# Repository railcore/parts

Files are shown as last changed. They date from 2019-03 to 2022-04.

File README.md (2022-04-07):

Railcore II 300ZL/ZLT
=======

RailCore® II is a Core-XY based Reprap 3D printer designed by J. Steve White & Tony Akens under the CC-Attribution Only license. Please refer to the attribution file for other contributions.

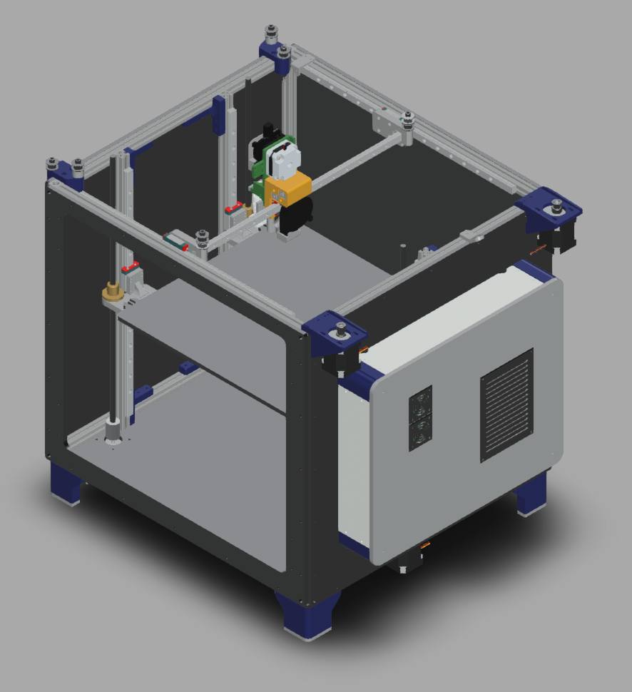
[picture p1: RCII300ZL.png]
Railcore


## Top-Level Specs
* CoreXY Motion System
* 300x300x300mm (ZL) or 300x300x600mm (ZLT) build volume.
* kinematically coupled bed plate (optionally)
* autotramming with 3-point bed-leveling
* ~$1700 for a single unit, including hotend. See the [BOM][bom] for the part breakdown
* User Extensible! We encourage extending the design to custom applications via custom tools and bed plates
* Full specs listed on [this page](https://railcore.org)

## Build your own Railcore

The best way to get started is to thumb through the [**Assembly Instructions**](https://railcore.dozuki.com/c/RailCore_II) and [**Bill of Materials**][bom] first. Then, your options are to self-source using the [BOM][bom], or purchase a kit. Kit options:

* https://www.filastruder.com/collections/railcore (US-Based, kits are comprised of exactly the parts on the [BOM][bom])
* https://hightemp3d.com (EU-Based, kits may not be comprised of the parts on the [BOM][bom])

## Repository Contents

* **DXF** - DXF files for the RailCore II 300ZL & ZLT, typically for sheet cutting. Materials that can be used are in a text materials.md file for viewing.
* **STEP**  - STEP files for the RailCore II 300ZL & ZLT. All printed parts, milled and cut parts.
* **STL**  - contains STL all the parts that need to be printed to produce a Railcore. Some, like Z-Brackets and Z-Yokes, are available in aluminum. See [BOM][bom].
* **auxillary**  - List of auxillary, untested or outdated parts for the RailCore II
  * **font** - contains the font used for the Railcore II 300ZL/ZLT engraving on the panels.
  * **jigs** - contains parts that can be used for alignment or assembly.
  * **print_tests** - contains parts that can be used for testing/tuning a Railcore
  * **outdated parts** - contains parts that are no longer used.
* **upgrade_or_crossgrade_parts** - for official parts that aren't necessary for a base RailCore functionality. (doors or STL's for commercial parts authorised by RailCore Labs)
* **wiring** - contains details on all the custom wiring that is used in a Railcore in WireViz format.

The halo and Y-plate are optional, the motor mount and idler mounts are recommended to be made from aluminum, but machined and finished versions are available, see [BOM][bom].
More printed parts are available at the [RailCore Thingiverse collection](https://www.thingiverse.com/railcore/collections/300zl-zlt)

## Support

Have questions? Building your own Railcore? **[Join the Discord!][discord]**
Lots more information available [here](https://railcore.org)

## Contributing

Railcore is meant to be extended by the community. If you are interested in contributing, there are a number of ways to get involved:

* Review, comment, or add to the **[open issues](https://github.com/railcore/parts/issues)**
* **[Join the Discord!][discord]**

### Open Source
The name Railcore is a registered trademark of RailCore Labs, LLC. All Rights reserved.
Railcore is licensed under a [Creative Commons Attribution-ShareAlike 3.0 Unported License][cc-by] (CC BY-SA 3.0).
[][cc-by]
You can modify / distribute these files, and as long as you attribute to RailCore Labs e.g. "Original design by RailCore Labs"

[bom]: https://docs.google.com/spreadsheets/d/1sxKl6h23SXfuNM7hNiX35rIrpISw8AruEEcNl2Fvibk/edit?usp=sharing
[cc-by]: https://creativecommons.org/licenses/by-sa/3.0/
[cc-by-image]: https://i.creativecommons.org/l/by-sa/3.0/88x31.png
[discord]: https://discord.gg/Sy569Hq
[wiki]: https://railcore.org

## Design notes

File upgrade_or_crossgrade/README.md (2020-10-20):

# Upgrade or Crossgrade Parts

This repo is for official parts that aren't necessary for a base RailCore functionality.

They may add functionality or improve appearance or provide different functionality from the base RailCore design, but are not necessary in any sense for building a RailCore. 

### Coupler Cover
This is a part designed to drop over the couplers to protect them from random detritus and tools - you know, the cruft in the bottom of your printer - from interfering or getting caught in your spinning Z couplers.

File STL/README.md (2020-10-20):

# Printed Parts

Here are the 3d printed parts necessary for a RailCore 2 printer. 

Some parts have been retired in favor of better alternatives from the community, and we recommend aluminum for the motor mounts, idler carriers, and X carriages; but the original designs still work and are archived here.

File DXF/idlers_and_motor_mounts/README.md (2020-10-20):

Aluminium & Printed idlers and motor mounts
Not needed if you have a halo

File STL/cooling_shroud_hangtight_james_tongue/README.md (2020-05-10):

Railcore V6 Part cooling Duct by Hangtight / James Tongue is licensed under the Creative Commons - Attribution - Non-Commercial license.
Railcore V6 Part cooling Duct V2 version with 3DCPrinting supports remixed by J.Steve White.
https://www.facebook.com/groups/RailCore/permalink/2262880700664343/

# Summary

A Beta part cooling duct for the Railcore 300ZL utilising a 5015 blower and proven nozzle geometry.

The adapter plate has a slot for a captive M3 nut, and the duct will require an insert/ helicoil for the blower retention bolt.

A duct version and adapter plate for the aluminium carriage plate added.

Both ducts revised to give an extra 2mm of height clearance. Spacers/shims added, and the F3d files are there for the adapters and shims.

http://creativecommons.org/licenses/by-nc/3.0/
http://www.thingiverse.com/thing:3367622

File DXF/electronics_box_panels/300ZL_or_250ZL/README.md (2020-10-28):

# 300ZL and 250ZL Electrobox

Some reorganization with a few changes:

* Removed unsightly vent holes from side panel of eBox
* Added snazzy ventilation to back panel for Astrydyne switch
* Added fancy fan holes to front panel
* Added bottom panel with cutouts for Z steppers (to keep fingers out of electronics)

Kits use HDPE largely; there are aluminum alternatives and lots of acrylic side panels out there. The original 250s were white melamine.

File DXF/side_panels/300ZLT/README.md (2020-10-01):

# ZLT Panels

*NB* : These files use the ../Electronics_Box! 

The *.dxf files here are exported from the base model.

Base panel includes bottom brace holes.
Right panel uses ZL Electrobox and has holes for Duet 2/Duex and Duet 3

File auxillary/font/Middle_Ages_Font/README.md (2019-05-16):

How to install this font on your computer
=========================================

For Windows 7 / Vista users:

- Right-click the font file(s) and choose "Install".

For users of the previous Windows versions:

- Copy the included file(s) into a default Windows font folder 
  (usually C:\WINDOWS\FONTS or C:\WINNT\FONTS)

For Mac users:

Mac OS X 10.3 or above (including the FontBook)

- Double-click the font file and hit "Install font" button at 
  the bottom of the preview.

Mac OS X

- Either copy the font file(s) to /Library/Fonts (for all users), 
  or to /Users/Your_username/Library/Fonts (for you only).

For Linux users:

- Copy the font file(s) to /USR/SHARE/FONTS

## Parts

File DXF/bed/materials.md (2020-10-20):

MIC6 or ACP5080P tool plate for the bed

0.6mm spring steel for the magnetic bed steel sheet.

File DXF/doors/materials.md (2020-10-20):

PC or clear acrylic for doors and covers
any plastic for the PSU & fan covers.

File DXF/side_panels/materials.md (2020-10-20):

Melamine MDF
Hardboard
Acrylic there are concerns it might crack around the bolts for mounting, washers may be advisable)
Masonite Pegboard
Plywood (hardwood such as birch is preferable. Plywood is deforms easily around bolts, washers and upgrading the “M3 x 10mm Hex head Bolts” to “M3 x 12mm Hex head Bolts” may be advisable)
Aluminum

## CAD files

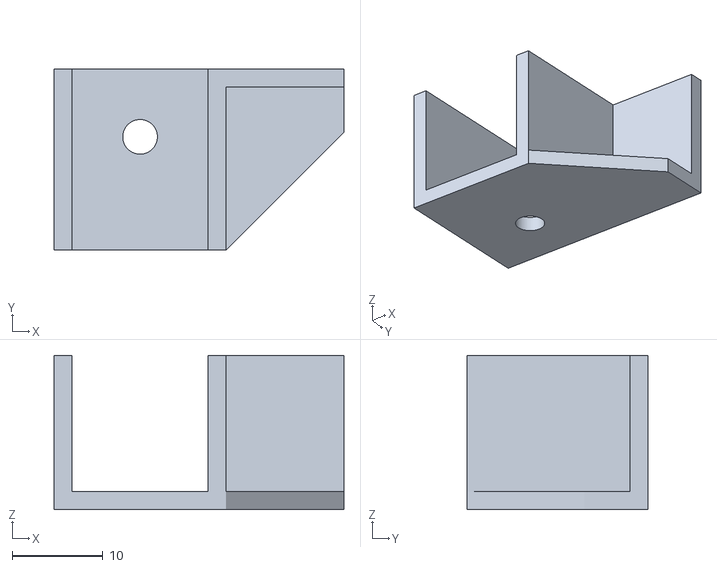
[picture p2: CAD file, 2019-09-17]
auxillary/jigs/Alignment_Jig/alignment_jig.stl
32.0 x 20.0 x 17.0

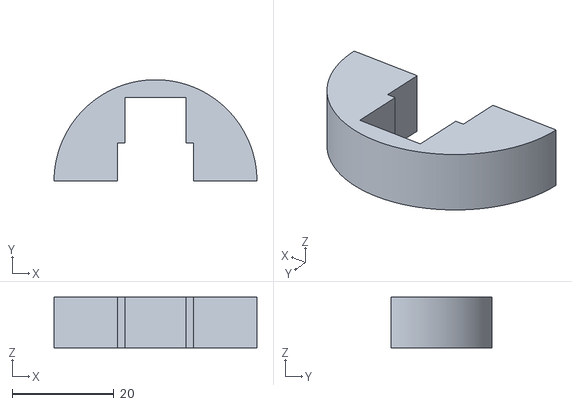
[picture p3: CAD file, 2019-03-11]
auxillary/jigs/Rail_Alignment_Tool.stl
40.0 x 20.0 x 10.0

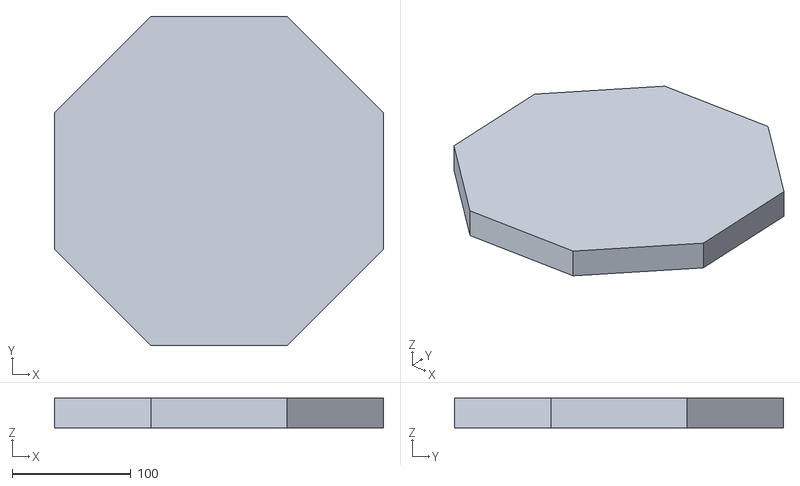
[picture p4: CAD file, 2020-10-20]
auxillary/print_tests/Octagon-v1.0.stl
277.2 x 277.2 x 25.0

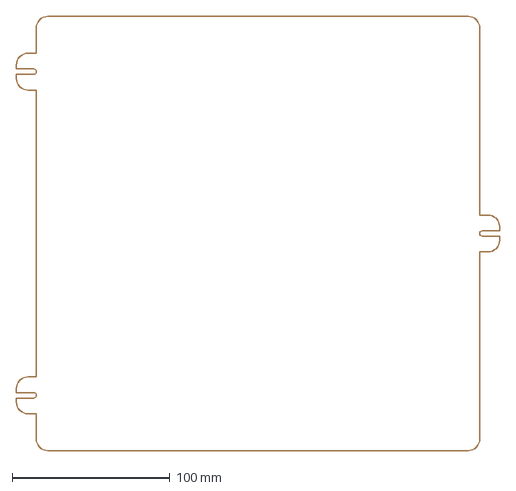
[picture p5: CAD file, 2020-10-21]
DXF/bed/250ZL_Bed v1.dxf
306.0 x 275.0 mm

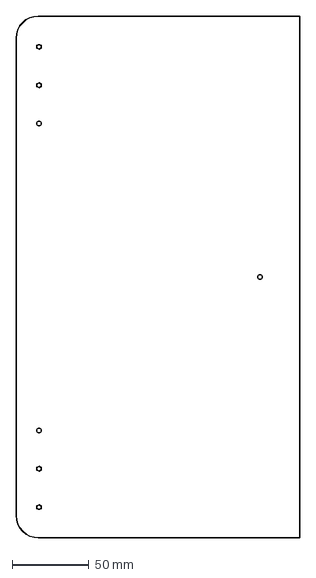
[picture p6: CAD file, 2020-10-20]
DXF/doors/250_Door.dxf
185.0 x 340.0 mm

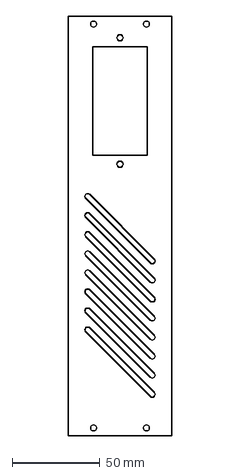
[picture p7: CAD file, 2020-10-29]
DXF/electronics_box_panels/300ZL_or_250ZL/300ZL_ElectroPanel_Rear_Astrodyne.dxf
59.0 x 238.9 mm

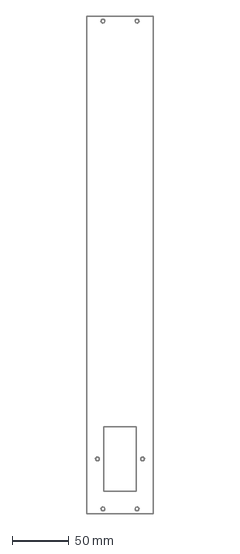
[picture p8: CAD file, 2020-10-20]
DXF/electronics_box_panels/300ZLT/300ZLT_ElectroPanel_Rear v1.dxf
59.0 x 438.9 mm

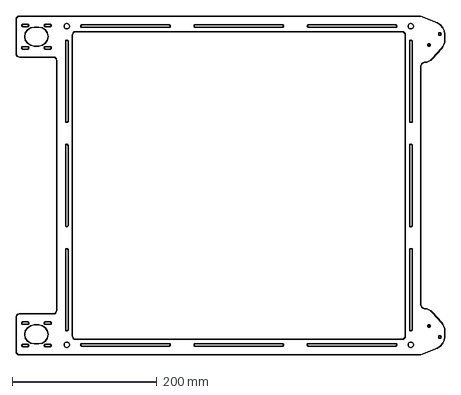
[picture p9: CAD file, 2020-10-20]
DXF/halo/Original_Halo-300ZL(T).dxf
591.7 x 467.7 mm

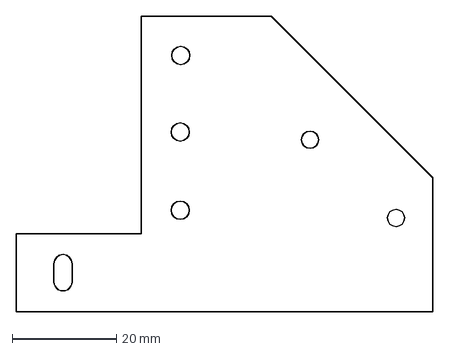
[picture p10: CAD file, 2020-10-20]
DXF/idlers_and_motor_mounts/Simple-idler-REAR-R1.DXF
80.0 x 56.7 mm

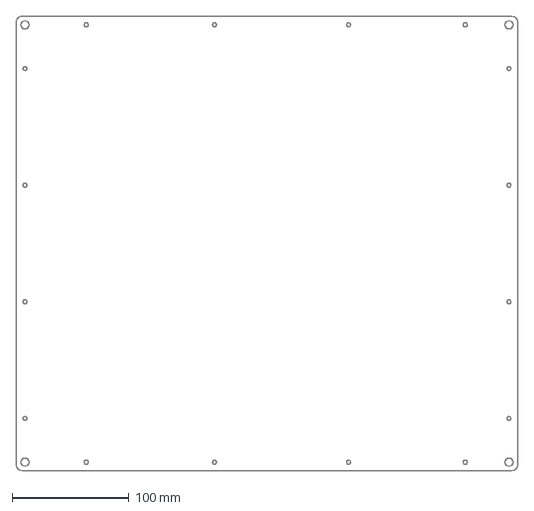
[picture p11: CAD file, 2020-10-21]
DXF/side_panels/250ZL/250ZL_Back_Panel_v1.dxf
430.0 x 390.0 mm

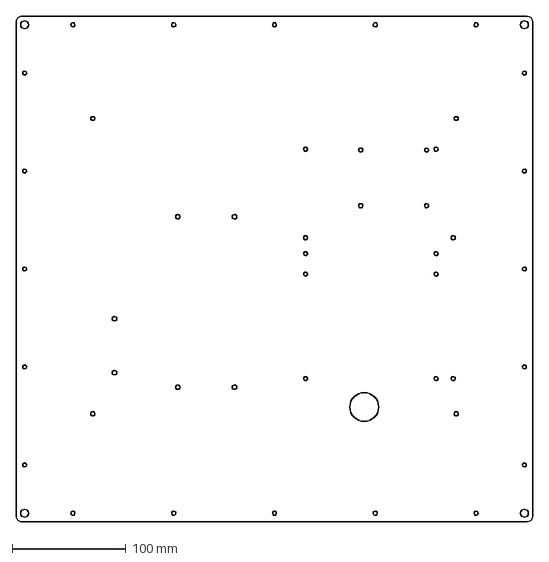
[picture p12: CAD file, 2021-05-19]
DXF/side_panels/300ZL/300ZL_Right_Panel.dxf
455.0 x 445.0 mm

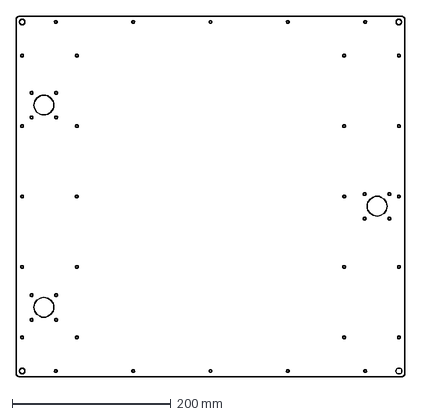
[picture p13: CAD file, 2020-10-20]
DXF/side_panels/300ZLT/300ZLT_Base_Panel.dxf
490.0 x 455.0 mm

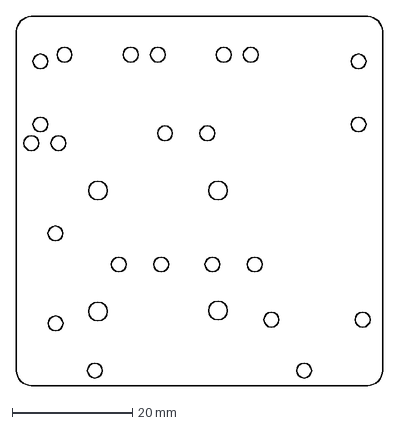
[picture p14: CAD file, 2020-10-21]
DXF/Y_plate/mrw-sdycarriage-rev4-hole-layout_mm.dxf
61.0 x 61.5 mm

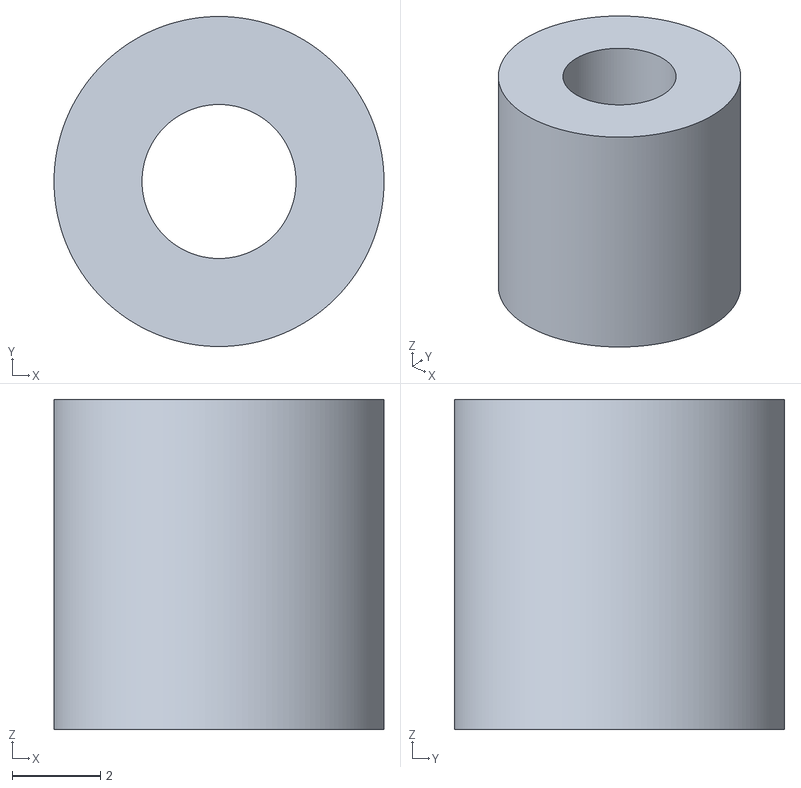
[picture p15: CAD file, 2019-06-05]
RailCore II Project Printed Parts/Duet_Standoff.stl
7.50 x 7.50 x 7.50

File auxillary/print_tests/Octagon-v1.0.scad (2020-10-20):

/* Simple octagon with flat surface facing the front of Railcore.  Season to taste. @Max_Plastix */

rotate ([0,0,45/2])
    cylinder (25,150,150, $fn=8);

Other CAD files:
STEP/250ZL_Bed v1.step
STEP/250ZL_panels/250ZL_Left_Panel_v1.step
STEP/300ZL_panels/300ZL_ElectroPanel_Rear_v1.step
STEP/300ZLT_panels/300ZLT_Back_Panel_v1.step
DXF/Y_plate/Simplified-Aluminum-Y-Plate.dxf
DXF/Y_plate/mrw-sdycarriage-rev4-hole-layout_original_inches.dxf
DXF/bed/300ZL_Bed_v1.dxf
DXF/bed/300ZL_bed_steel_sheet.dxf
DXF/doors/300_Door1.dxf
DXF/electronics_box_panels/300ZLT/300ZL(T)_ElectroPanel_Top_v1.dxf
DXF/electronics_box_panels/300ZLT/300ZLT_ElectroGuard_v1.dxf
DXF/electronics_box_panels/300ZLT/300ZLT_ElectroGuard_v1_built_in_vents.dxf
DXF/electronics_box_panels/300ZLT/300ZLT_ElectroPanel_side_v1.dxf
DXF/electronics_box_panels/300ZL_or_250ZL/300ZL_ElectroGuard_built_in_vents.dxf
DXF/electronics_box_panels/300ZL_or_250ZL/300ZL_ElectroGuard_v1.dxf
DXF/electronics_box_panels/300ZL_or_250ZL/300ZL_ElectroPanel_Bottom.dxf
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

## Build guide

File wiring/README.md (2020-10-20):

The wiring.yml file is processed by WireViz

https://github.com/formatc1702/WireViz

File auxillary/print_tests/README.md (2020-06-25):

### Squared circle by JohnOCFII

### Acceleration Test piece
The 5mm marks are helpful to combine changes. 0 infill, 2 perimeter, no top, no bottom. Brim helps to stick.

### Retraction Test by kraegar
https://www.thingiverse.com/thing:1642140
Just a test object to try and balance retraction settings. The round base shows Z-Scar (zits, blobs, etc). The small towers show stringing and underextrusion due to rapid retracts. You can measure the small towers with a set of calipers to test under extrusion. They should not get thinner as they get taller.

### Ringing Test by jstevewhite
https://www.thingiverse.com/thing:2866393

Print Settings
* Rafts:No
* Supports:No
* Resolution: .1 or .2
* Infill:15%

### Ripple tests by MaxPlastix

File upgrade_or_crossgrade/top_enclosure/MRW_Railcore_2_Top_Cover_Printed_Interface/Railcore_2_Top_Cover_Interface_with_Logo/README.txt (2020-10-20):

Railcore 2 Top Cover Interface with Logo by burntcrispy on Thingiverse: https://www.thingiverse.com/thing:4269353

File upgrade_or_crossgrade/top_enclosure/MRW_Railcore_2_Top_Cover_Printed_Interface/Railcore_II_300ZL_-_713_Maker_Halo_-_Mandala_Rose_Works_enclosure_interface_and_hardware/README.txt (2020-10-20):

Railcore II 300ZL - 713 Maker Halo - Mandala Rose Works enclosure interface and hardware. by theMachinista on Thingiverse: https://www.thingiverse.com/thing:4259224

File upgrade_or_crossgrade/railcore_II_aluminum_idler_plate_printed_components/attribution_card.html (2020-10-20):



# RailCore II Aluminum Idler Plate Printed Components by kraegar

## Published on December 6, 2018

### www.thingiverse.com/thing:3262662

####  

#### Creative Commons - Attribution

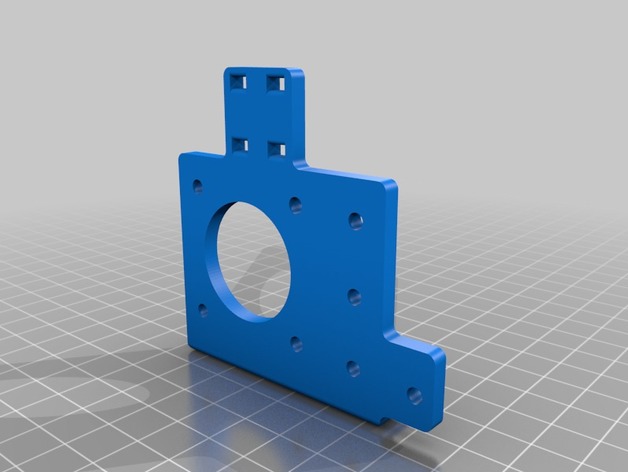
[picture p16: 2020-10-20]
upgrade_or_crossgrade/railcore_II_aluminum_idler_plate_printed_components/images/627aa86716e27f85e7522cbee6491515_preview_featured.jpg

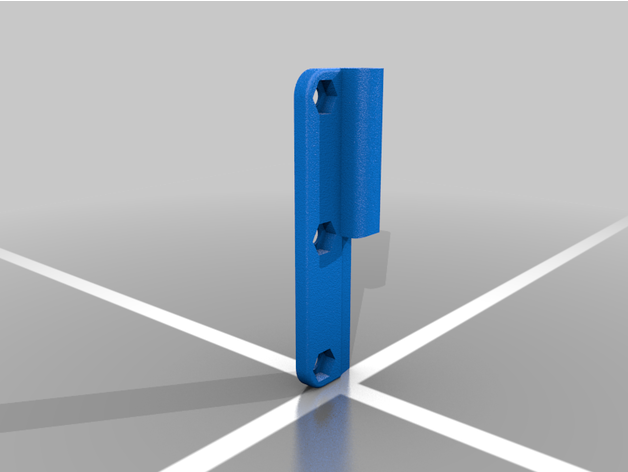
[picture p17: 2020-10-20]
upgrade_or_crossgrade/top_enclosure/MRW_Railcore_2_Top_Cover_Printed_Interface/Railcore_II_300ZL_-_713_Maker_Halo_-_Mandala_Rose_Works_enclosure_interface_and_hardware/images/Right_Panel_Hinge.png

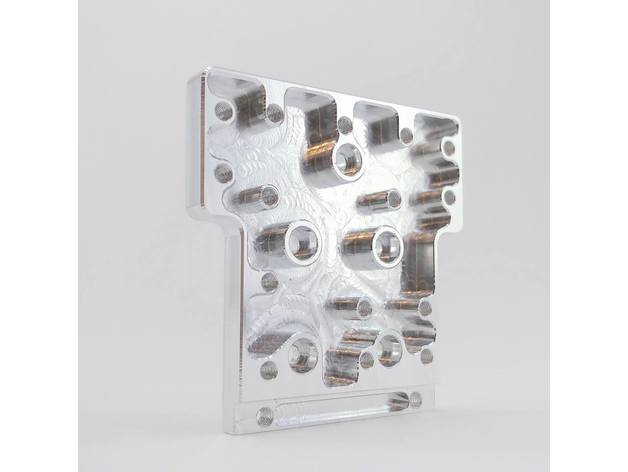
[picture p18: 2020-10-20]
upgrade_or_crossgrade/railcore_II_aluminum_idler_plate_printed_components/images/b67c66722f65eed7974716dabab80873_preview_featured.jpg

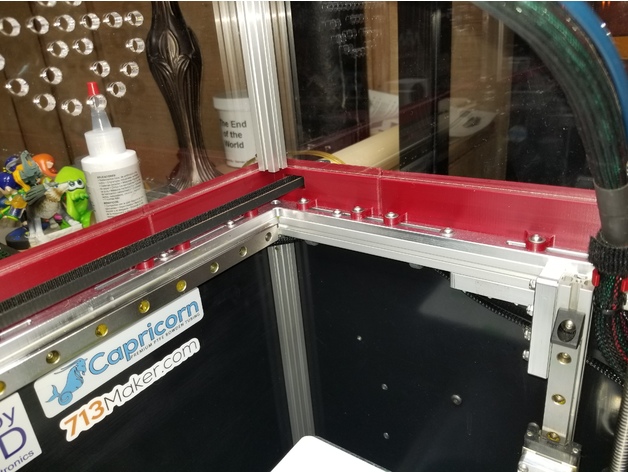
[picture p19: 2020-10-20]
upgrade_or_crossgrade/top_enclosure/MRW_Railcore_2_Top_Cover_Printed_Interface/Railcore_II_300ZL_-_713_Maker_Halo_-_Mandala_Rose_Works_enclosure_interface_and_hardware/images/20200403_143359.jpg

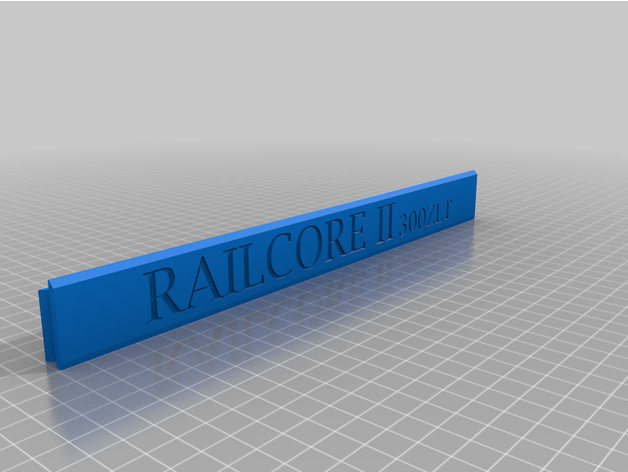
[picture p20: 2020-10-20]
upgrade_or_crossgrade/top_enclosure/MRW_Railcore_2_Top_Cover_Printed_Interface/Railcore_II_300ZL_-_713_Maker_Halo_-_Mandala_Rose_Works_enclosure_interface_and_hardware/images/Side_Front_ZLT.png

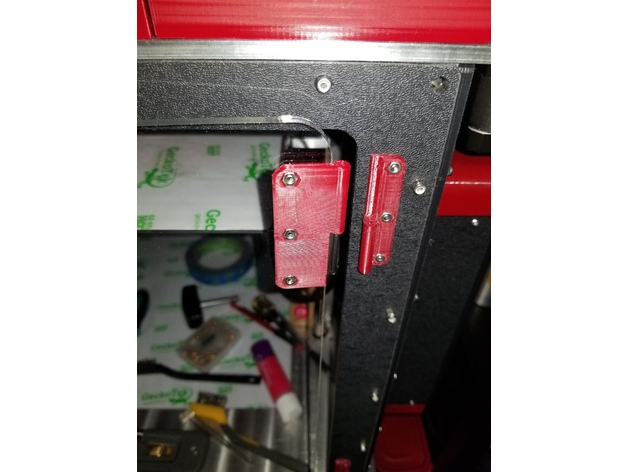
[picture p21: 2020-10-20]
upgrade_or_crossgrade/top_enclosure/MRW_Railcore_2_Top_Cover_Printed_Interface/Railcore_II_300ZL_-_713_Maker_Halo_-_Mandala_Rose_Works_enclosure_interface_and_hardware/images/20200403_142231.jpg

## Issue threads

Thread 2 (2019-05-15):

Avoiding head crashes by reversing yokes.

dandancheeseandham, 2019-05-15:
Steve L

> So I had a head fan crash tonight.  Kinda bad. As the carriage moved to the left and then to 0,0 home, the 40mm Noctura Fan with @jstevewhite  slim fan shroud, the entire fan got pulled away, breaking the shroud and pulling a wire out of my hot end thermister.
>
> BUT i found an elegant solution. It's only cost me a small amount of Z-Height.  I took the bed off, then removed BOTH of the left Z yokes.  I reversed the yokes so the rail car is now below the bed plane, and the vertical part of the yokes are also pointing downward instead of upward.  This gives me MUCH more room on the left size so no more fan crashes!

[pic1](https://media.discordapp.net/attachments/546187906033909792/578038665541058600/image1.jpg)
[pic2](https://media.discordapp.net/attachments/546187906033909792/578038666178461717/image0.jpg)

I think this is worth considering. Lose Z height, gain X where the Z extrusions are.

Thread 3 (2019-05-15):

Upgrade to 450mm X rails

dandancheeseandham, 2019-05-15:
Because longer will fit and more X-travel will result.

lostapathy, 2019-05-15:
If one is just buying "off the shelf" rails, they should definitely do 450mm.

If one is buying premium rails from misumi etc where the cost difference for custom length is minimal, we should probably should recommend people order them to match the x-extrusion length to fill it up.  I don't see a downside, and it would prevent ever running carriages past the end of the rail.

dandancheeseandham, 2019-05-15:
FYI, Misumi provide 395,420 and 445mm sizes.
The only custom length one need be the Y rail as that needs to be exactly 400mm

dandancheeseandham, 2019-05-17:
> I don't see a downside, and it would prevent ever running carriages past the end of the rail.

To play devils advocate with you:
I don't have an issue here with that. I have stops at each end (which also reduce the amount of X distance on my 400mm rails) and my hotend can still travel the full length of the bed.
https://i.imgur.com/bSMXZIV.jpg

Is there a reason you don't have any kind of stop? Would that just be a solution? Do you rails need placing better?

dandancheeseandham, 2019-05-24:
I've been having a good mull about this. I think that the HiWin values should stay as is for cost , and it is what is necessary to do the job.
However 420 can be recommended for Misumi (or just as an enhancement) in the docs, with a note explaining it is also a benefit for <x> reasons.

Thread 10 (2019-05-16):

Bottom panel for electronics enclosure

lostapathy, 2019-05-16:
The electronics enclosure should have a bottom panel to keep stray fingers away from mains wiring.

I am currently running a printed one.  I will get the file published for feedback/use by others.  Longer-term, this should really be a standard part CNC cut with the other side panels.

dandancheeseandham, 2019-05-16:
I've added "Electro Bottom Panel-Printed Solid.dxf" to

\railcore\parts\ElectronicsBoxZL
\railcore\parts\ElectronicsBoxZLT

it's been cut and is on my ZLT

lostapathy, 2019-05-16:
The panel I'm running is at https://www.thingiverse.com/thing:3634362

It's designed with some stiffening ribs to hold up better as a printed part.  I like that it's got ventilation slots in it to allow airflow, but does not have the relatively large opening in the dxf linked above, as that seems like it'd still allow fingers.

In a perfect world we'd get a CNC-cut panel included in the panel kits with a similar design.

dandancheeseandham, 2019-05-16:
Added to parts. Nice one.

dandancheeseandham, 2019-05-16:
Actually, I'm using two blank sides, and the large opening bottom panel has been used with the intent to design a cover for that hole, which allows the z axis steppers, and incorporates the power socket for power into it

dandancheeseandham, 2019-05-16:
(so when done, they can be a pair)

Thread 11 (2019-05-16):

Larger electronics enclosure

lostapathy, 2019-05-16:
It would be quite helpful if the electronics enclosure on the 300ZL was larger.  There seems to be ample real estate to do it and I'm not sure of any compelling reason not to.

Doing so would allow us to make the wiring tidier as well as improve our options for better isolating/shielding the wiring (or at least terminals) that carry mains voltage.  I designed some parts for guarding the power supply terminals, but actual assembly was problematic in the current enclosure (issue #9 should help that, though).

It appears we could expand the enclosure 25-30mm toward the front and back and 50mm vertically lower and still fit comfortably, as well as still allow the cover panel to be cut from the waste piece out of the machine's front panel.

Obviously this could be made available in future panel sets by just cutting them for the new enclosure size.  We could also develop a retrofit kit that includes the updated electronics box panels as well as printable corners that use the new panels but still mount to the old holes so that older railcores don't need new mounting holes cut.

kraegar, 2019-05-16:
The electronics panel is sized so it can easily and efficiently be cut out
of the scrap of the front panel.  I'm not positive of Joe's milling layout,
but enlarging it may actually end up increasing the kit costs due to more
HDPE use / waste, and additional milling time.

On Thu, May 16, 2019 at 10:43 AM Joe Francis <notifications@github.com>
wrote:

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

lostapathy, 2019-05-16:
> The electronics panel is sized so it can easily and efficiently be cut out
of the scrap of the front panel.

Maybe I wasn't 100% clear as submitted, but I actually did measure mine and there's quite a bit of room for growing this cover and still cutting it from the waste.

It appears the electronics box was sized for the 250ZL and not scaled up when the 300ZL was designed.

kraegar, 2019-05-16:
There's likely room to expand it some, but at least in how I milled it, it
wasn't as much as you'd think because you need good workholding on that
scrap in between the front panel layout and the Electronics panel. If you
can't hold that scrap securely the edges on the panels really shows it.
Especially with how narrow that front panel is already.  HDPE moving or
vibrating at all kills the surface finish. I can talk with Joe about it and
how his milling setup compares to what I did, but we'd need to be careful
to keep with something that doesn't cause problems.

You're right it was originally sized for the 250.  It was sized so it could
be laser cut out of the 250 scrap, that meant I couldn't mill it out of
that scrap, and had to use other material to do the 250's electronics
panels, which was a major headache.

On Thu, May 16, 2019 at 11:06 AM Joe Francis <notifications@github.com>
wrote:

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

dandancheeseandham, 2019-05-16:
> The electronics panel is sized so it can easily and efficiently be cut out of the scrap of the front panel. I'm not positive of Joe's milling layout, but enlarging it may actually end up increasing the kit costs due to more HDPE use / waste, and additional milling time.

Oh! I did not realise that this was a design constraint! I guess because your photo, and a lot of photos from self-builders (so selection bias there admittedly) have all had acrylic electronics enclosures. Now I think about it, the kit builders do use all HDPE.
It makes sense to reduce waste.

I'm torn though, as a ZLT owner, it's also bloody awesome to have plenty of room 😄. If a bit more room can be eked out, (and just 1mm added to each side becomes 1324mm^2 in area) and I'm sure it would be appreciated by the new kit builders and self-builders alike.

dandancheeseandham, 2019-05-16:
Yeah. Understood. I think it is realised that this is more of an involved upgrade than most.

lostapathy, 2019-05-16:
> Yeah. Understood. I think it is realised that this is more of an involved upgrade than most.

Correct - that's why I tagged as "railcore 2.5" as per the discussion on #4

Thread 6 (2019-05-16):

E-stop in case of Z probing failure

dandancheeseandham, 2019-05-16:
Head crashes seem to be the major worry for people.

So how about micro-switch emergency stop on the print head, in a location 1mm lower than the users existing probe.

Bonus points for adding 2 more micro-switches in series:
 * one located at Z max , so if Z max is exceeded somehow (this is pretty optional and almost certainly unneeded)
 * one as an emergency stop button on the frame (this is optional, but seems quite nice)

What type of emergency stop is up for debate. However with RTOS I'm fairly happy with just triggering M112/M999.

TheeDynamikOne, 2021-01-19:
I think the best solution for this would be an Emergency stop button, just like other machines that can damage themselves when things go wrong. Adding redundancy is a slippery slope when you're also adding the possibility of another failure mode.

lostapathy, 2021-01-19:
> Adding redundancy is a slippery slope when you're also adding the possibility of another failure mode.

To be fair, so long as the e-stops are wired in series, you'd fail stopped rather than "fail to stop", which is perfectly ok.

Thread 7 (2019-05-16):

Bottom Y braces (and the holes in the panels) standard in build

dandancheeseandham, 2019-05-16:
They seem to be a popular add-on.

By adding holes in the bottom panel in F360 for the brace, it sets a standard distance, laser cut or milled precisely so the extrusion is definitely straight.

That way also, additional mods such as https://www.thingiverse.com/thing:3629939 can also be standardised somewhat.

lostapathy, 2019-05-16:
I agree - even if @Project-R3D doesn't want to include the additional extrusions in the kit, it'd be great to get the holes cut so they are in a standardized location.

I am biased because I designed the part linked above, but I think the spacing it relies on is ideal and more or less the "standard" people who have done it by hand have shot for as well.

Project-R3D, 2019-05-16:
We are working with the RailCore Labs Team on our mid year update which will include these extra extrusions in the kits.

lostapathy, 2019-05-16:
Awesome!  Can we get the layout documented sooner rather than later so that people retrofitting can be compatible?  Preferably based on the above-linked part if it's not yet set in stone.

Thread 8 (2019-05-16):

Replace standard fan in F360 and BOM with James Tongue Cooling shroud.

dandancheeseandham, 2019-05-16:
Is this possible?

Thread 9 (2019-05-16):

Utilize more heatset inserts on electronics box corners

lostapathy, 2019-05-16:
Right now it's quite a lot of work to take any of the side panels off the electronics enclosure since they are all secured with nuts and bolts and access to the nuts is challenging.

Electronics box corners that used heatset inserts for all screws would make it possible to remove any side of the panel individually.

This would make it a lot easier to remove the front panel to gain access to the SD card, for one example.

lostapathy, 2019-07-16:
Published an STL for this https://www.thingiverse.com/thing:3748830

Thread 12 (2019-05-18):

Expand size of wiring cutouts in top of electronics enclosure.

lostapathy, 2019-05-18:
The wiring cutouts in the top panel of the electronics corner are extremely tight if one sleeves the cables and runs additional cables through the cutouts.

I have the cords for PanelDue, front stepper, and a filament out sensor all running through the front slot.  All are sleeved, and they end up pinched in fairly tightly.  Expanding this slot a little bit would be a big help for people with similarly built-out machines.

dandancheeseandham, 2019-09-19:
What sort of size would you suggest?

kraegar, 2019-09-19:
It's fairly trivial to ream out the HDPE for a larger cutout if needed.
It's much harder to reduce the hole for those that don't.

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

lostapathy, 2019-09-20:
I think just expanding the radius of the cutouts from 7.5mm to 10mm would get the job done and not make the holes seem excessive.

If I were messing with that part, I would also see what it looks like to put a small (like 1mm) radius on the currently-sharp ends of that slot, just to eliminate a sharp point that can snag wires during assembly.

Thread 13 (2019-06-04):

Add Nylon spacers to the BOM for the Duet and Duex5

dandancheeseandham, 2019-06-04:
As title. Self-sourcers can get stuck on that bit if they don't have standoffs "in stock"

kraegar, 2019-06-04:
Should likely just upload the printable ones I've been using and add them
to the parts list.

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

lostapathy, 2019-06-04:
I made some brackets with heat-set inserts on both sides so that you can screw the brackets through the side panel and then screw the duet/duex into the bracket.  Makes assembly a lot easier than spacers and nuts - might be something we should entertain "upstream" as well?

kraegar, 2019-06-04:
I've considered modeling a duet + duex5 "holder" that has integrated wire
minders, so it tidies it all up nicely.  But it's been "on the list" for
over a year now.

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

dandancheeseandham, 2019-06-05:
@kraegar printable ones will be a reasonable step to start with. Do you have a link to the ones you used to save me digging through Thingiverse?
They can then be added to the parts repo and to the docs

kraegar, 2019-06-05:
Added to thingiverse and the BOM parts list

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

dandancheeseandham, 2019-06-05:
Nice one. I've added that to the parts repo too.

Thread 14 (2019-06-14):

Add clearance hole to foot for access to bottom corner cube

veng1, 2019-06-14:
The bottom screws in the frame are accessible via holes in the bottom panel until the feet are installed.  A clearance hole through the foot would fix that.
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

[Foot with clearance hole v2.f3d.zip](https://github.com/railcore/parts/files/3290950/Foot.with.clearance.hole.v2.f3d.zip)

veng1, 2019-06-14:
Dan,

Am I supposed to do anything with this or is it simply informational?

Thanks,

Pat.

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

--
Patrick H. Ryan, Jr.
President
Venture Engineering Corporation
770-604-9677
404-580-2568 (Mobile)

dandancheeseandham, 2019-09-19:
@veng1 you don't need to do anything. We're working on methods of getting fixes upstreamed, so collating the information at this point is the most useful thing we can do!

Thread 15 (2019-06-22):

PanelDue 5 no longer available from Filastruder; substitute PanelDue 5i

SteveDallas, 2019-06-22:
Affects: 300 ZL and 300 ZLT BOMs.

The non-integrated PanelDue and 5" display combination is no longer available from Filastruder, so the BOM link doesn't get you to the right part.

This link is for the PanelDue 5i with a 1 meter 4 pin cable:
https://www.filastruder.com/products/paneldue-5i?variant=12524929876039

The price is $89.99

dandancheeseandham, 2019-09-19:
@SteveDallas Thank you. Done!

Closed 2019-09-19.

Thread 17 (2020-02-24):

Parts Missing from Printed Parts List tab in BOM

SteveDallas, 2020-02-24:
affects 250ZL, 300ZL, 300ZLT BOMs

The parts 40mm_Fan_Cover and PSU_Vent_Cover are missing from the Printed Parts List tab in the various BOMs.

Also, the list of "printed parts not needed" that appears in the 250ZL BOM on the ZL Build Differences tab, should probably be included somewhere in the 300ZL and ZLT BOMs, so that self-sourcers don't print unneeded parts if they aren't following all the documentation too closely.

Closed 2021-12-06.

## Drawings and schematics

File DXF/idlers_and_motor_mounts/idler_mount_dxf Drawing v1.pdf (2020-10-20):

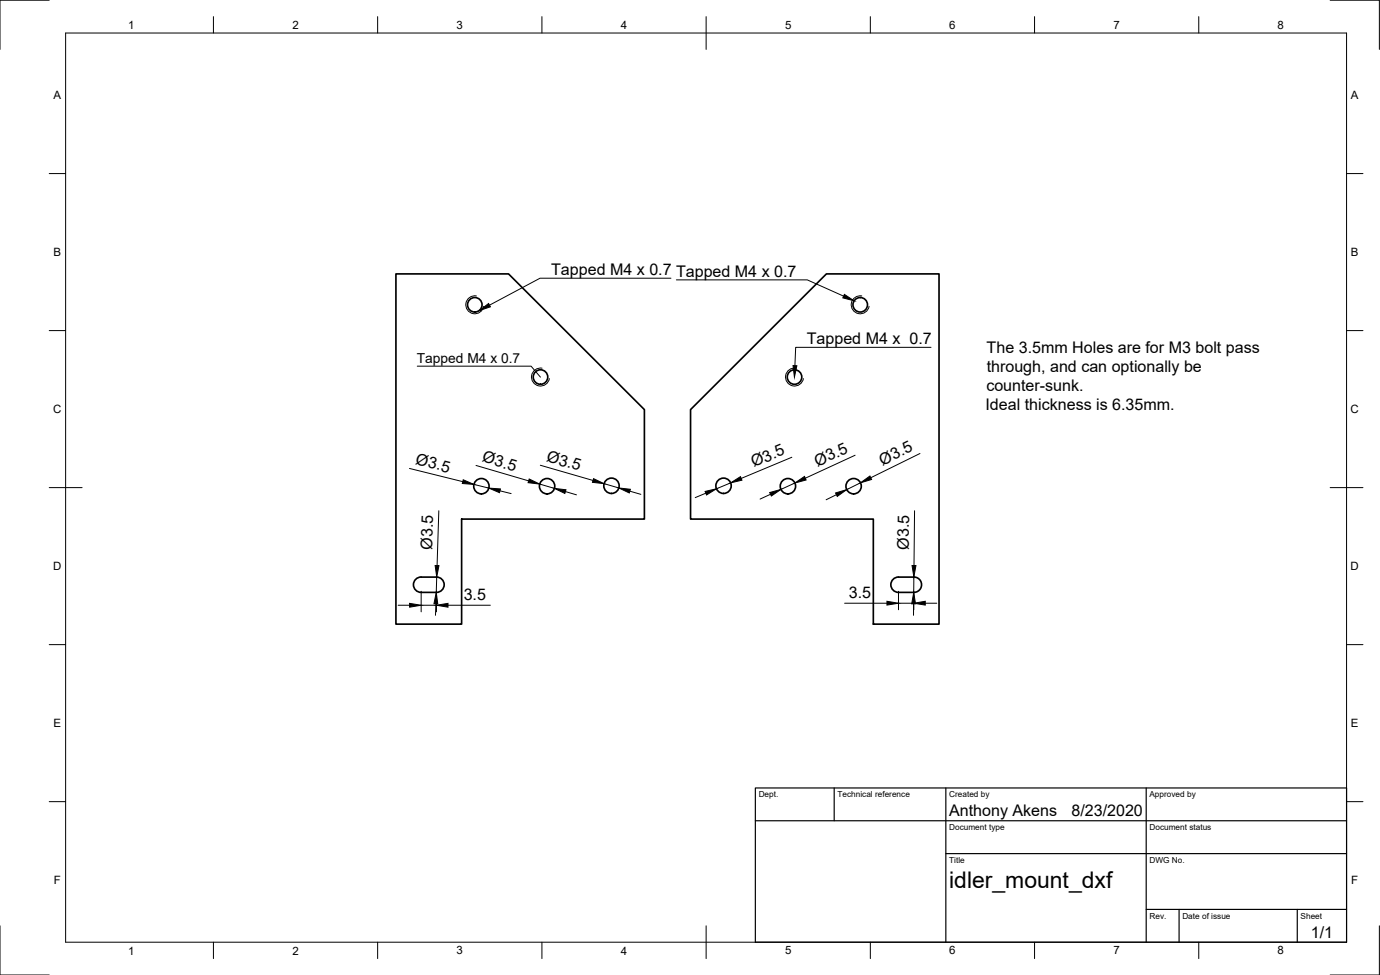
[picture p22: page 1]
Tapped M4 x 0.7; Tapped M4 x 0.7 Tapped M4 x 0.7; The 3.5mm Holes are for M3 bolt pass

through, and can optionally be
counter-sunk.
Ideal thickness is 6.35mm.

Dept. | Technical reference | Created by Anthony Akens 8/23/2020 | Approved by

Document type | Document status

Title idler_mount_dxf | DWG No.

Rev. | Date of issue | Sheet 1/1

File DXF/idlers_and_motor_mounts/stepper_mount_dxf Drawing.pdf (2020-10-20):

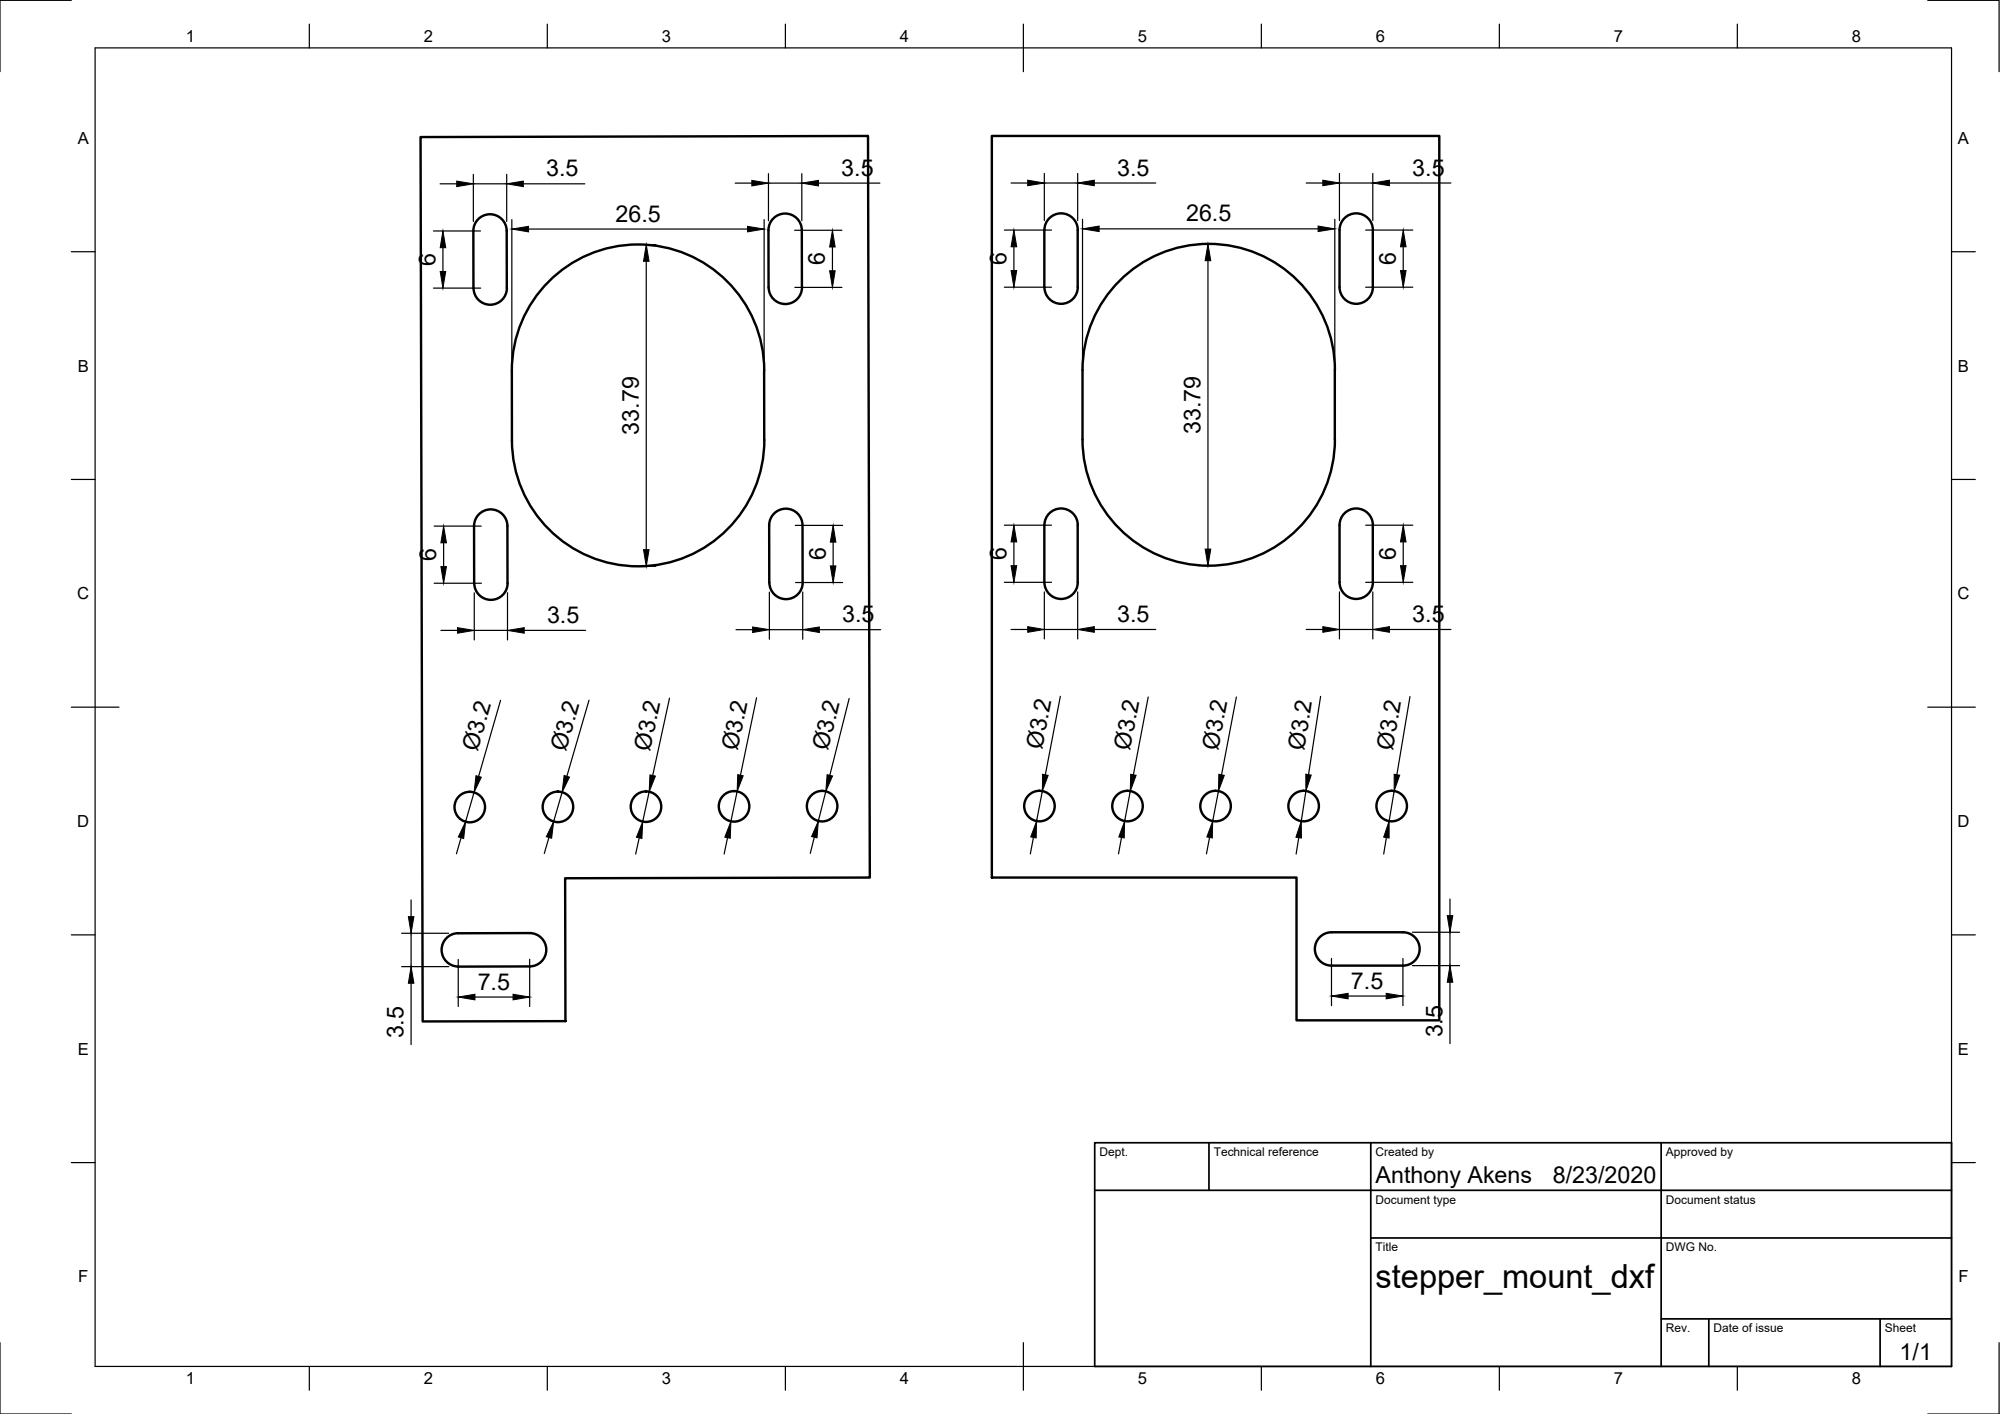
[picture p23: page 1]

Dept. | Technical reference | Created by Anthony Akens 8/23/2020 | Approved by

Document type | Document status

Title stepper_mount_dxf | DWG No.

Rev. | Date of issue | Sheet 1/1

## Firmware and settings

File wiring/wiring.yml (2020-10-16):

connectors:
  X1:
    pinout: [SSR3]
    type: Ring Terminal
    subtype: insulated
    notes: "Label: SSR3"
  X2:
    pinout: [SSR4]
    type: Ring Terminal
    subtype: insulated
    notes: "Label: SSR4"
  F_10_1: # manually define a ferrule (with unique designator)
    category: ferrule
    type: Ferrule, crimp
    notes: Duet Bed+
  F_10_2: # manually define a ferrule (with unique designator)
    category: ferrule
    type: Ferrule, crimp
    notes: Duet Bed-
    
  X3:
    pinout: [PSU 24v-]
    type: Ring Terminal
    subtype: insulated
    notes: "Label: PSU 24v-"
  F_10_3: # manually define a ferrule (with unique designator)
    category: ferrule
    type: Ferrule, crimp
    notes: Duet Vin-
  F_10_4: # manually define a ferrule (with unique designator)
    category: ferrule
    type: Ferrule, crimp
    notes: Duet Vin-

    
  X4:
    pinout: [Chassis GND]
    type: Ring Terminal
    subtype: insulated
    notes: "Label: Chassis GND"
  F_10_5: # manually define a ferrule (with unique designator)
    category: ferrule
    type: Stripped Wire, 10mm
    notes: WAGO Ground Block

  X5:
    pinout: [PSU 24v+]
    type: Ring Terminal
    subtype: insulated
    notes: "Label: PSU 24v+"
  F_10_6: # manually define a ferrule (with unique designator)
    category: ferrule
    type: Ferrule, crimp
    notes: Duet Vin+

  X6:
    pinout: [PSU 24v+]
    type: Ring Terminal
    subtype: insulated
    notes: "Label: PSU 24v+"
  F_10_7: # manually define a ferrule (with unique designator)
    category: ferrule
    type: Ferrule, crimp
    notes: Duex Vin+

  X7:
    pinout: [SSR1]
    type: Ring Terminal
    subtype: insulated
    notes: "Label: SSR1"
  F_10_8: # manually define a ferrule (with unique designator)
    category: ferrule
    type: Stripped Wire, 10mm
    notes: WAGO AC Hot Block

  X8:
    pinout: [PSU AC/L]
    type: Ring Terminal
    subtype: insulated
    notes: "Label: PSU AC/L"
  F_10_9: # manually define a ferrule (with unique designator)
    category: ferrule
    type: Stripped Wire, 10mm
    notes: WAGO AC Hot Block
    
  X9:
    pinout: [Power Inlet Hot]
    type: 0.25" Quick Disconnect
    subtype: insulated
    notes: "Label: Power Inlet Hot"
  F_10_10: # manually define a ferrule (with unique designator)
    category: ferrule
    type: Stripped Wire, 10mm
    notes: WAGO AC Hot Block
    
  X10:
    pinout: [PSU AC/N]
    type: Ring Terminal
    subtype: insulated
    notes: "Label: PSU AC/N"    
  F_10_11: # manually define a ferrule (with unique designator)
    category: ferrule
    type: Stripped Wire, 10mm
    notes: WAGO AC Neutral Block
    
  X11:
    pinout: [Power Inlet Neutral]
    type: 0.25" Quick Disconnect
    subtype: insulated
    notes: "Label: Power Inlet Neutral"
  F_10_12: # manually define a ferrule (with unique designator)
    category: ferrule
    type: Stripped Wire, 10mm
    notes: WAGO AC Neutral Block

  X12:
    pinout: [PSU GND]
    type: Ring Terminal
    subtype: insulated
    notes: "Label: PSU GND"
  F_10_13: # manually define a ferrule (with unique designator)
    category: ferrule
    type: Stripped Wire, 10mm
    notes: WAGO AC Ground Block
    
  X13:
    pinout: [Power Inlet Ground]
    type: 0.25" Quick Disconnect
    subtype: insulated
    notes: "Label: Power Inlet Ground"
  F_10_14: # manually define a ferrule (with unique designator)
    category: ferrule
    type: Stripped Wire, 10mm
    notes: WAGO AC Ground Block
    
  X14:
    type: Molex KK 254
    subtype: female
    pinout: [SIG, n/a, GND]
    notes: "Label: X-endstop"
  X15:
    pinout: [COM, NO, NC]
    type: OMRON D2F-01F 
    subtype: Microswitch

  X16:
    type: Molex KK 254
    subtype: female
    pinout: [GND, n/a, SIG]
    notes: "Label: Y-endstop"
  X17:
    type: Molex KK 254
    subtype: female
    pinout: [FAN-, V_Fan]
    notes: "Label: Part Cooling Fan"
  X18:
    type: Molex 70107-0003
    subtype: male
    pinout: [FAN-, V_FAN, GND, SIG]
    notes: "Label: Fan&Endstop"

  X19:
    pinout: [NC, NO, COM]
    type: OMRON D2F-01F 
    subtype: Microswitch
  X20:
    type: Delta BFB0524HH Fan
    pinout: [Fan-, FAN+]
  X21:
    type: Molex 50-57-9404
    subtype: female
    pinout: [FAN-, V_FAN, GND, SIG]
    notes: "Label: Fan&Endstop"

  X22:
    pinout: [PSU GND]
    type: Ring Terminal
    subtype: insulated
    notes: "Label: Bed Ground"
  F_10_15: # manually define a ferrule (with unique designator)
    category: ferrule
    type: Stripped Wire, 10mm
    notes: WAGO AC Ground Block
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

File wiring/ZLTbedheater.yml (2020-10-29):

connectors:
  X1:
    type: NTC 100K thermistor, 3950K
    subtype: female
    pinout: [Thermistor, Thermistor]
  X2:
    type: Dupont 2-pin female
    subtype: female
    pinout: [Thermistor, Thermistor]
    notes: "Label: Bed Thermistor"  

    
  X3:
    type: 750w Silicone Heater
    pinout: [Heater, Heater]
    
  X4:
    pinout: [SSR]
    type: Ring Terminal
    subtype: insulated

  F_10_5: # manually define a ferrule (with unique designator)
    category: ferrule
    type: Stripped Wire, 10mm




cables:
  W1:
    category: bundle # bundle
    length: 1.0
    gauge: 24 AWG
    colors: [RD, RD] # custom colors, wirecount is implicit
  W2:
    category: bundle # bundle
    length: 1.0
    gauge: 16 AWG
    colors: [WH] # custom colors, wirecount is implicit
  W3:
    category: bundle # bundle
    length: 1.24
    gauge: 16 AWG
    colors: [WH] # custom colors, wirecount is implicit
  W17:
    category: bundle # bundle
    length: 1.25
    gauge: 16 AWG
    colors: [GN] # custom colors, wirecount is implicit



connections:
  - # attach ferrules
    - X1: [1,2]
    - W1: [1,2]
    - X2: [1,2]

  - # attach ferrules
    - X3: [1]
    - W2: [1]
    - X4: 1
  - # attach ferrules
    - X3: [2]
    - W3: [1]
    - F_10_5: 1

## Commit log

2019-03-11 Added RailCore II parts
    [300ZLT_Bearing_Block.stl, 40mm_Fan_Cover.stl, BLTouch_Mount.stl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]
2019-03-12 added aluminium parts
    [Alu_Back_X_Carriage v1 v3.step, Alu_Front_X_Carriage v1 v3.step, Back_X_Carriage v1.iges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]
2019-05-16 add electronics box guard
    [Electro Bottom Panel-Printed Solid.dxf, Electro Guard.dxf, Electro Rear Panel.dxf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]
2019-05-16 renaming and additions
    [Electronics Box - Bottom Panel (Printed Solid).dxf, Electronics Box - Guard.dxf, Electronics Box - Side Panel Front.dxf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]
2019-05-16 added lostapathys bottom panel
    [electronics-box-bottom-printable.stl]
2019-05-16 added bottom printable panel by lostapathy
    [Electro Bottom Panel-Printed Solid.dxf, ZL - Back Panel.dxf, ZL - Bottom Panel.dxf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]
2019-06-05 Added Duet standoff
    [Duet_Standoff.stl]
2019-09-17 added alignment jig
    [alignment_jig.stl, alignment_jig_mirror.stl]
2019-09-18 top enclosure addition
    [180_mm.stl, 267_mm.stl, 302_mm.stl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]
2019-12-21 added cheeseandham electronic box
    [Electronics Box - Bottom Panel (Printed Solid).dxf, Electronics Box - Guard.dxf, Electronics Box - Side Panel Front.dxf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]
2020-03-12 cheeseandham halo parts
    [NEMA23 and Magnum halo.stl, cheeseandham_halo.dxf]
2020-06-25 Add octagon test for vertical wall Ripple
    [Octagon-v1.0.scad, Octagon-v1.0.stl]
2020-08-16 Updating DXFs to match the model on F360
    [ZL - Back Panel.dxf, ZL - Bottom Panel.dxf, ZL - Front Panel.dxf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]
2020-08-16 Motor Nacelles to reduce leakage through the printed interface.
    [FinalNacell.stl]
2020-08-16 Cleaning up printed parts
    [300ZLT_Bearing_Block.stl, 40mm_Fan_Cover.stl, BLTouch_Mountv4.f3d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]
2020-08-20 Added holes for Duet 3 and RPi
    Updating to include holes for Duet 3 and RPi.
    [ZL- Right Panel.dxf]
2020-08-20 File cleanup
    [ZL - Right Panel.dxf, ZL- Right Panel.dxf]
2020-08-20 Cleaning up whitespace in filenames
    [ZL_ Left_Panel.dxf, ZL_Back_Panel.dxf, ZL_Bottom_Panel.dxf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]
2020-08-20 Cleaning up more whitespaces in filenames
    [180_mm.stl, 267_mm.stl, 300ZLT_Bearing_Block.stl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]
2020-08-20 More cleanup
    [180_mm.stl, 267_mm.stl, 300ZLT_Bearing_Block.stl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]
2020-08-20 Adding panel DXFs from RailCore Labs design drawing.
    [ZL_EBox_Back_Panel_Astrodyne.dxf, ZL_EBox_Back_Panel_Bulgin.dxf, ZL_EBox_Front_Panel.dxf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]
2020-08-22 Added upgrade/crossgrade folder and threw in Coupler Covers and a README.md
    [CouplerCover.stl]
2020-08-28 Updated ZLT panels from master model.
    [300ZLT_Back_Panel.dxf, 300ZLT_Base_Panel.dxf, 300ZLT_Front_Panel.dxf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]
2020-09-17 Adding wiring specifications
2020-10-01 Cleaning up repo
    [Display-Back.stl, Display-Spacer.stl, Electronics Box - Bottom Panel (Printed Solid).dxf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]
2020-10-14 Added Modified EBox corner
    Committing ebox corner that can be printed without supports.
    [ModifiedEBoxCorner.stl]
2020-10-14 Moved Ebox_Corner-Alternate_Supportless to Auxilliary and outdated
    [Ebox_Corner-Alternate_Supportless_v1.stl]
2020-10-14 Moved to Auxilliary
    [Ebox_Corner-Alternate_Supportless_v1.stl]
2020-10-14 Removing obsolete Mosquito mount
    [Mosquito_Groove_Mount_v3.stl]
2020-10-14 Added printed Mosquito Groove Mount
    [Mosquito_Groove_Mount.stl]
2020-10-16 major reorg
    [180_mm.stl, 250_Door.dxf, 267_mm.stl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]
2020-10-18 Moving cable clip to main folder
    [cable_clip.stl]
2020-10-18 removing moved file
    [cable_clip.stl]
2020-10-19 latest additions
    [Ebox_Corner-Alternate_Supportless_v1.stl, ModifiedEBoxCorner.stl, Mosquito_Groove_Mount.stl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]
2020-10-19 motor mounts
    [Motor-mount-Front-V1-SW-SIMPLE.DXF, Motor-mount-V2-rear-V1-SW-SIMPLE.DXF, Simple-idler-FRONT-R1.DXF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]
2020-10-20 Move Y carriage and update README
    [Simplified-Aluminum-Y-Plate.dxf, mrw-sdycarriage-rev4-hole-layout.dxf]
2020-10-21 250ZL STEP files and groove mounts
    [250ZL_Back_Panel_v1.step, 250ZL_Bed v1.dxf, 250ZL_Bed v1.step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]
2020-10-21 250ZL dxfs added
    [250ZL_Back_Panel_v1.dxf, 250ZL_Bottom_panel.dxf, 250ZL_Front_Panel_v1.dxf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]
2020-10-21 additional STEP & STL files
    [180_mm.stl, 250ZL_Bed v1.step, 267_mm.stl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]
2020-10-28 Fixing up electrobox DXFs
    [#300ZL_ElectroPanel_Rear_Astrodyne.dxf, 300ZL_ElectroGuard_built_in_vents.dxf, 300ZL_ElectroGuard_v1.dxf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]
2020-10-29 Fixed switch mount holes to match @ 3.5mm
    [300ZL_ElectroPanel_Rear_Astrodyne.dxf]
2020-10-29 adding bed heater wiring
2021-05-19 Add files via upload
    Updated panel from new sketch to fix hole alignment on duet3 mount, parametric design in fusion.
2024-05-17 Rename DXF/f3z/RailCore II 300ZL - Nov 2019.f3z to F3Z/RailCore II 300ZL - Nov 2019.f3z
    [RailCore II 300ZL - Nov 2019.f3z]
2024-05-17 Rename DXF/f3z/RailCore II 300ZLT.f3z to F3Z/RailCore II 300ZLT.f3z
    [RailCore II 300ZLT.f3z]
2024-05-17 Rename DXF/f3z/RailCoreII-ZL v1.f3z to F3Z/RailCoreII-ZL v1.f3z
    [RailCoreII-ZL v1.f3z]

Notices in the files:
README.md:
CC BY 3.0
